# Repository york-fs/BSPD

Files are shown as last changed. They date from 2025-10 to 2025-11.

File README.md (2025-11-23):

# Brake System Plausibility Device







Uses non-programmable logic to implement the Brake System Plausibility Device required by FSUK rules. The BSPD opens the low-voltage shutdown circuit in the event of current being delivered to the motor while hard braking occurs.

## Features
- TODO

## PCB Notes
- Designed in KiCad 9.0

BSPDv1 3

## Cloning

A recursive clone must be used to download the `kicad-library` repository:

    git clone --recursive https://github.com/york-fs/bspd.git

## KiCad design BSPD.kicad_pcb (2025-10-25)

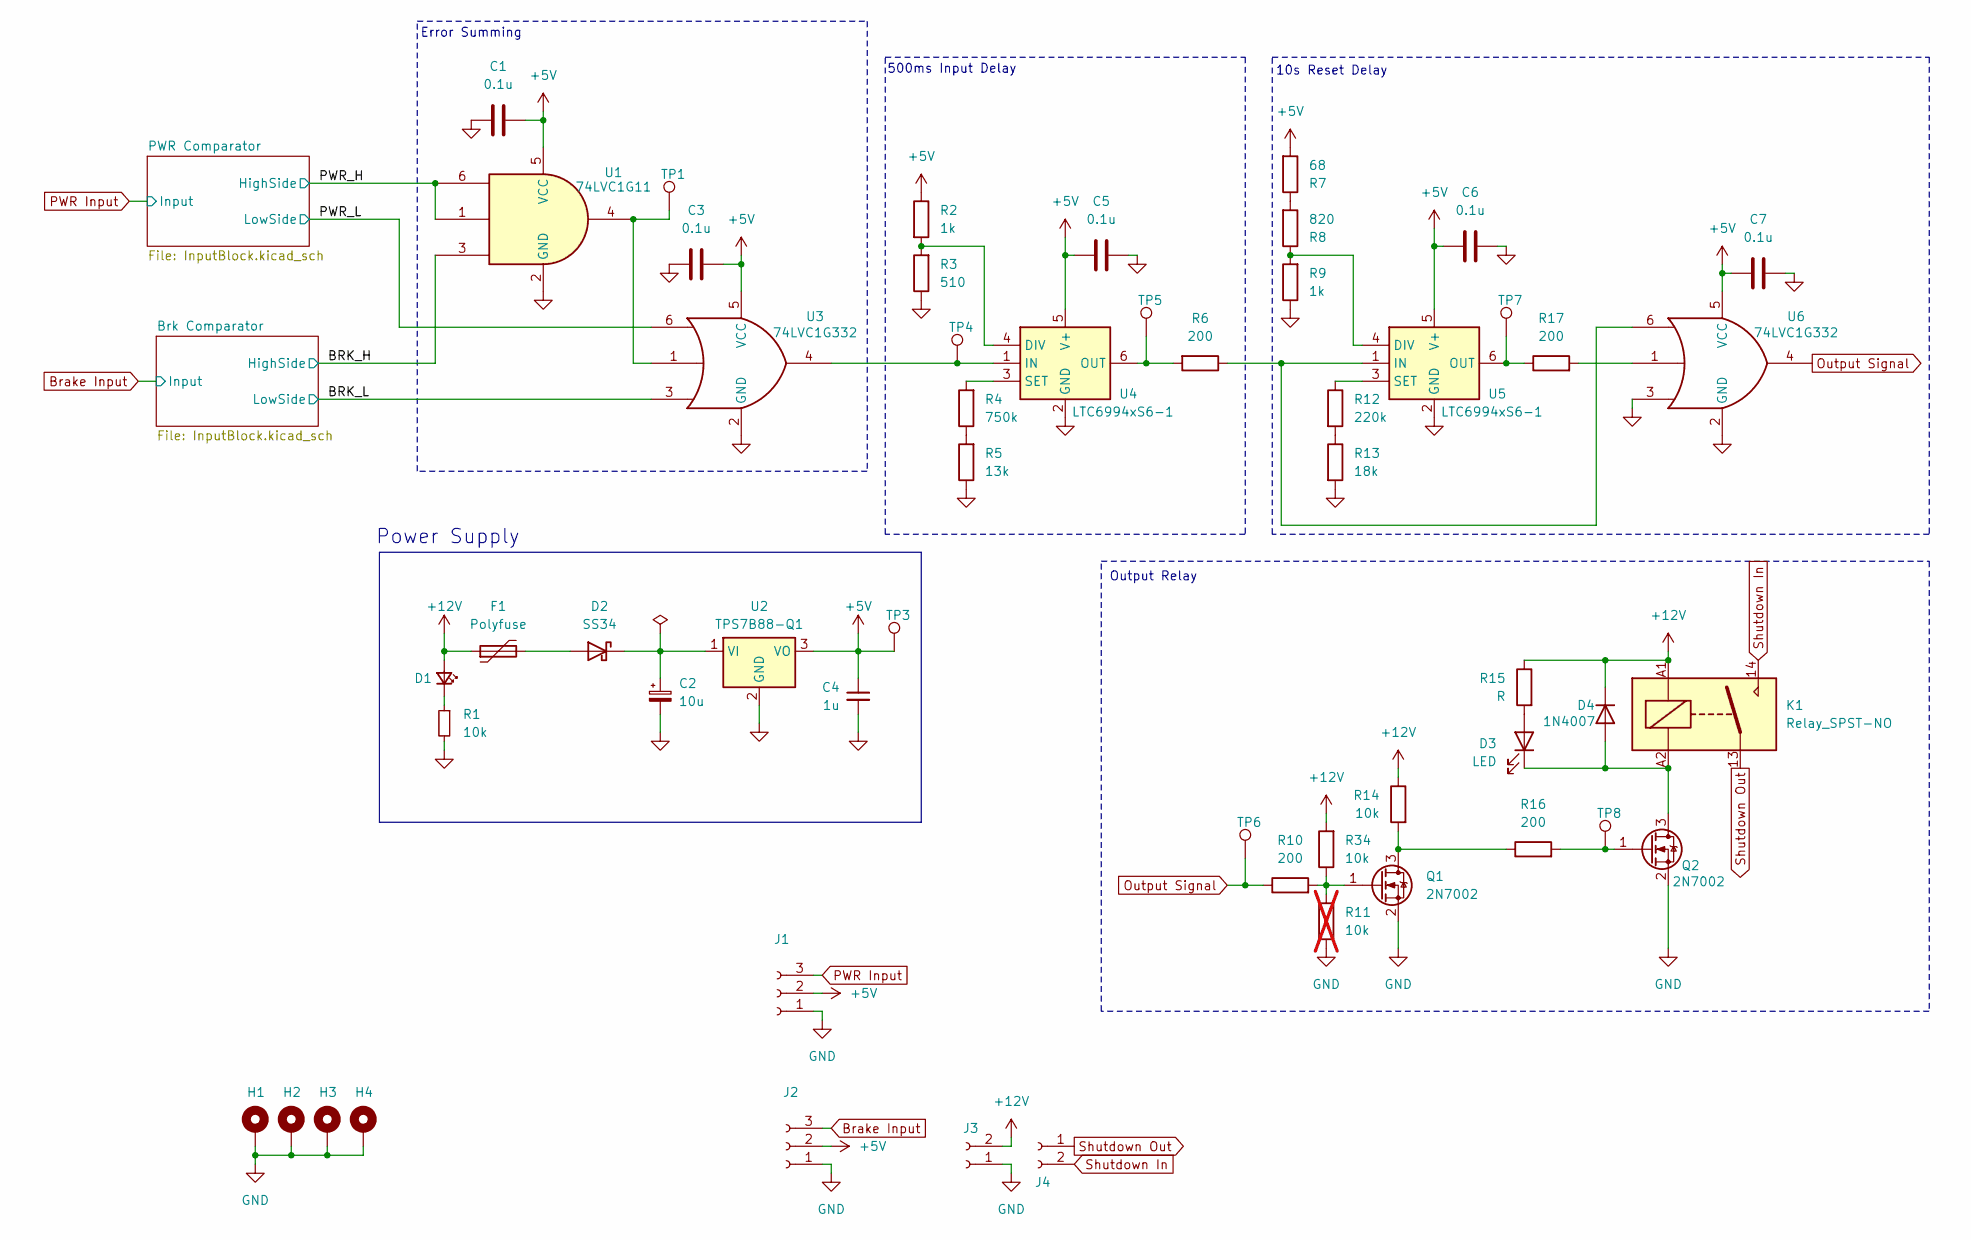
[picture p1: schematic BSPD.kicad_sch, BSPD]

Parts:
C1, C3, C5, C6, C7: 0.1u; C_0603_1608Metric
C2: 10u; CP_Elec_6.3x5.4
C4: 1u; C_0603_1608Metric
D1: LED_Small; LED_0603_1608Metric
D2: SS34; D_SMA
D3: LED; LED_0603_1608Metric
D4: 1N4007; D_SOD-123F
F1: Polyfuse; R_0805_2012Metric
H1, H2, H3, H4: MountingHole_Pad; MountingHole_3.2mm_M3_Pad_Via
J1, J2: Conn_01x03_Socket; MolexMicrofitPlus1x3
J3, J4: Conn_01x02_Socket; MolexMicrofitPlus1x2
K1: Relay_SPST-NO; Relay_SPST_Omron_G2RL-1A
Q1, Q2: 2N7002; SOT-23
R1, R14, R34: 10k; R_0603_1608Metric
R2, R9: 1k; R_0603_1608Metric
R3: 510; R_0603_1608Metric
R4: 750k; R_0603_1608Metric
R5: 13k; R_0603_1608Metric
R6, R10, R16, R17: 200; R_0603_1608Metric
R7: 68; R_0603_1608Metric
R8: 820; R_0603_1608Metric
R11: 10k; R_0603_1608Metric; not fitted
R12: 220k; R_0603_1608Metric
R13: 18k; R_0603_1608Metric
R15: R; R_0603_1608Metric
TP1, TP3, TP4, TP5, TP6, TP7, TP8: TestPoint; TestPoint_Keystone_5000-5004_Miniature
U1: 74LVC1G11; SOT-23-6
U2: TPS7B88-Q1; TO-252-2
U3, U6: 74LVC1G332; SOT-23-6
U4, U5: LTC6994xS6-1; TSOT-23-6

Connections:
+5V: C1.1, C3.1, C4.1, C5.2, C6.1, C7.1, J1.2, J2.2, R2.1, R7.2, TP3.1, U1.5 (VCC), U2.3 (VO), U3.5 (VCC), U4.5 (V+), U5.5 (V+), U6.5 (VCC); also elsewhere on the board
+12V: D1.2 (A), D4.1 (K), F1.1, J3.2, K1.A1, R14.1, R15.1, R34.2
/BRK_H: U1.3; also elsewhere on the board
/BRK_L: U3.3; also elsewhere on the board
/PWR_H: U1.1, U1.6; also elsewhere on the board
/PWR_L: U3.6; also elsewhere on the board
Brake Input: J2.3; also elsewhere on the board
GND: C1.2, C2.2, C3.2, C4.2, C5.1, C6.2, C7.2, H1.1, H2.1, H3.1, H4.1, J1.1, J2.1, J3.1, Q1.2 (S), Q2.2 (S), R1.2, R3.1, R5.1, R9.1, R11.2, R13.2, U1.2 (GND), U2.2 (GND), U3.2 (GND), U4.2 (GND), U5.2 (GND), U6.2 (GND), U6.3; also elsewhere on the board
unnamed: D1.1 (K), R1.1
unnamed: D2.2 (A), F1.2
unnamed: C2.1, D2.1 (K), U2.1 (VI)
unnamed: D3.2 (A), R15.2
unnamed: D3.1 (K), D4.2 (A), K1.A2, Q2.3 (D)
unnamed: Q1.3 (D), R14.2, R16.1
unnamed: Q1.1 (G), R10.2, R11.1, R34.1
unnamed: Q2.1 (G), R16.2, TP8.1
unnamed: R4.1, R5.2
unnamed: R7.1, R8.2
unnamed: R12.2, R13.1
unnamed: R17.2, U6.1
unnamed: TP1.1, U1.4, U3.1
unnamed: R2.2, R3.2, U4.4 (DIV)
unnamed: TP4.1, U3.4, U4.1 (IN)
unnamed: R6.2, TP5.1, U4.6 (OUT)
unnamed: R4.2, U4.3 (SET)
unnamed: R8.1, R9.2, U5.4 (DIV)
unnamed: R6.1, U5.1 (IN), U6.6
unnamed: R17.1, TP7.1, U5.6 (OUT)
unnamed: R12.1, U5.3 (SET)
Output Signal: R10.1, TP6.1, U6.4
PWR Input: J1.3; also elsewhere on the board
Shutdown In: J4.2, K1.14
Shutdown Out: J4.1, K1.13

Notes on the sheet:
500ms Input Delay
Error Summing
Power Supply
10s Reset Delay
Output Relay

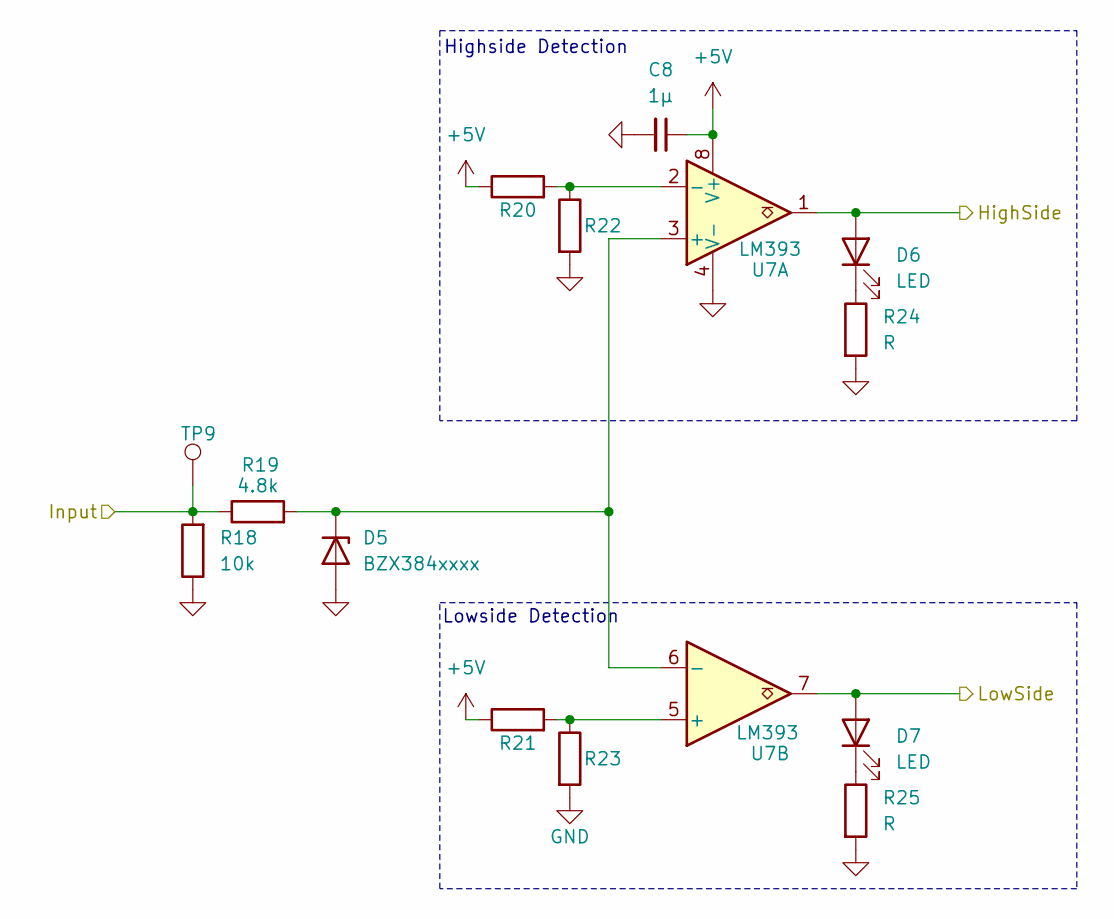
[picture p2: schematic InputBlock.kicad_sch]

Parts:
C8: 1µ; C_0603_1608Metric
D5: BZX384xxxx; D_SOD-323
D6, D7: LED; LED_0603_1608Metric
R18: 10k; R_0603_1608Metric
R19: 4.8k; R_0603_1608Metric
R20, R21: 39K; R_0603_1608Metric
R22, R23: 62k; R_0603_1608Metric
R24, R25: R; R_0603_1608Metric
TP9: TestPoint; TestPoint_Keystone_5000-5004_Miniature
U7: LM393; SOIC-8_3.9x4.9mm_P1.27mm

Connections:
+5V: C8.1, R20.1, R21.1, U7.8 (V+); also elsewhere on the board
/PWR_H: D6.2 (A), U7.1; also elsewhere on the board
/PWR_L: D7.2 (A), U7.7; also elsewhere on the board
GND: C8.2, D5.2 (A), R18.1, R22.2, R23.2, R24.2, R25.2, U7.4 (V-); also elsewhere on the board
unnamed: D5.1 (K), R19.2, U7.3 (+), U7.6 (-)
unnamed: D6.1 (K), R24.1
unnamed: D7.1 (K), R25.1
unnamed: R20.2, R22.1, U7.2 (-)
unnamed: R21.2, R23.1, U7.5 (+)
PWR Input: R18.2, R19.1, TP9.1; also elsewhere on the board

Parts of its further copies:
C9: 1µ; C_0603_1608Metric
D8: BZX384xxxx; D_SOD-323
D9, D10: LED; LED_0603_1608Metric
R26: 10k; R_0603_1608Metric
R27: 4.8k; R_0603_1608Metric
R28, R29: 39K; R_0603_1608Metric
R30, R31: 62k; R_0603_1608Metric
R32, R33: R; R_0603_1608Metric
TP10: TestPoint; TestPoint_Keystone_5000-5004_Miniature
U8: LM393; SOIC-8_3.9x4.9mm_P1.27mm

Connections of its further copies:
+5V: C9.1, R28.1, R29.1, U8.8 (V+); also elsewhere on the board
/BRK_H: D9.2 (A), U8.1; also elsewhere on the board
/BRK_L: D10.2 (A), U8.7; also elsewhere on the board
Brake Input: R26.2, R27.1, TP10.1; also elsewhere on the board
GND: C9.2, D8.2 (A), R26.1, R30.2, R31.2, R32.2, R33.2, U8.4 (V-); also elsewhere on the board
unnamed: D8.1 (K), R27.2, U8.3 (+), U8.6 (-)
unnamed: D9.1 (K), R32.1
unnamed: D10.1 (K), R33.1
unnamed: R28.2, R30.1, U8.2 (-)
unnamed: R29.2, R31.1, U8.5 (+)

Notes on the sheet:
Highside Detection
Lowside Detection

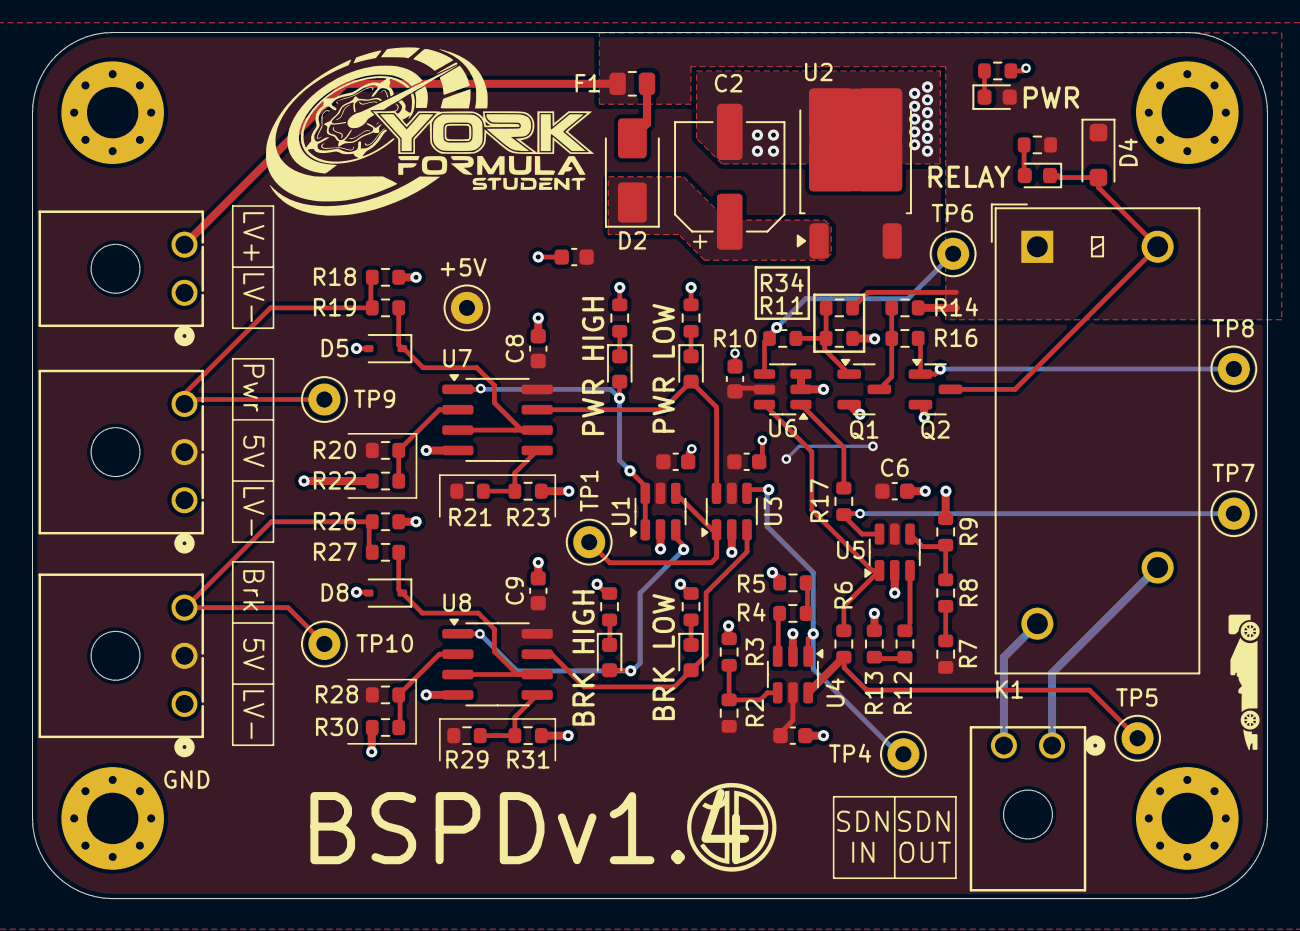
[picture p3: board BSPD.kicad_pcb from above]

Board: 2 copper layers, 77.0 x 54.0 mm, 82 parts (0 on the bottom side), 43 nets.

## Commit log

2025-10-03 Initial commit v1.3
    [BSPD.kicad_pcb, BSPD.kicad_sch, bom.csv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]
2025-10-05 Updated production gerbers
    Reversed shutdown connector
    Added back test points 1 and 2
    Fixed shutdown connector placement
    [BSPD.kicad_pcb, BSPD.kicad_sch, bom.csv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]
2025-10-23 V1.4
    Replaced Comparators for push pull (not yet selected)
    Changed input block to 5V
    Added more test points
    Changed Zener Package
    Moved Diodes to active high
    [BSPD.kicad_pcb, BSPD.kicad_sch, InputBlock.kicad_sch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]
2025-10-23 Cleaned up repo
    [BSPD.kicad_pcb, BSPD.kicad_sch, InputBlock.kicad_sch]
2025-10-23 Linked footprint library
2025-10-25 kicad-library: Update to latest version
2025-10-25 Updated connector colours
    [BSPD.kicad_pcb]
2025-10-25 project: Add footprint library
2025-10-25 Updated footprints
    [BSPD.kicad_pcb]
2025-11-23 ci: Add kicad workflow
